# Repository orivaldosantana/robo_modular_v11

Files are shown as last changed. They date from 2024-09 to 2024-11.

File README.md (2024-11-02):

# Robô Modular - RM
Repositório de código, peças 3D e especificações básicas para o robô modular.

## Introdução

Esta versão é construída com Arduino, motor DC, baterias 18650 e ponte H L9110.
URA

## Peças 3D 
### STLs: 
* 1 x [Suporte Arduino](https://github.com/orivaldosantana/robo_modular_v11/blob/main/partes%203D/suporte%20arduino.stl) 
* 1 x [Base do suporte L9110](https://github.com/orivaldosantana/robo_modular_v11/blob/main/partes%203D/sup%20L9110%20base.stl)
* 1 x [Topo do suporte L9110](https://github.com/orivaldosantana/robo_modular_v11/blob/main/partes%203D/sup%20L9110%20topo.stl)
* 2 x [Suporte Motor DC](https://github.com/orivaldosantana/robo_modular_v11/blob/main/partes%203D/suporte%20motor%20v2.stl)
* 1 x [Chapa Modular 7x7](https://github.com/orivaldosantana/robo_modular_v11/blob/main/partes%203D/chapa%207x7.stl) 
* 2 x [Tira Modular 7x1](https://github.com/orivaldosantana/robo_modular_v11/blob/main/partes%203D/tira%207%20furos.stl) 
* 1 x [Caixa ultrassom](https://github.com/orivaldosantana/robo_modular_v11/blob/main/partes%203D/caixa%20ultrassom.stl)
* 1 x [suporte da caixa do ultrassom](https://github.com/orivaldosantana/robo_modular_v11/blob/main/partes%203D/suporte%20caixa%20ultrassom.stl)
* 4 x [Espaçador de 32 mm](https://github.com/orivaldosantana/robo_modular_v11/blob/main/partes%203D/espa%C3%A7ador%2032mm.stl)
* 2 x [Espaçador de 28 mm](https://github.com/orivaldosantana/robo_modular_v11/blob/main/partes%203D/espa%C3%A7ador%2028mm.stl)
* 1 x [Suporte para o sensor de linha](https://github.com/orivaldosantana/robo_modular_v11/blob/main/partes%203D/suporte%20sensor%20linha.stl)
* 1 x [Suporte roda boba](https://github.com/orivaldosantana/robo_modular_v11/blob/main/partes%203D/roda%20omni/sup%20omni.stl)
* 1 x [Roda Omni](https://github.com/orivaldosantana/robo_modular_v11/tree/main/partes%203D/roda%20omni)

### Editaveis no OnShape
## Montagem
* [Link para a montagem](https://cad.onshape.com/documents/1797a3ca0f50067e5b2f7467/w/d2fdd87127a878d32b85a5d1/e/55e155fb02a23330101a4e5d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)

Cima MD

MD

MD

MD

## Montagem Motores 
* [Preparação dos motores DC](https://youtu.be/uoehkZviNMs)
* [Montagem dos motores DC](https://youtu.be/0yrsRWZnIXw)

### Parafusos e complementares 
Entre chassis e suporte Arduino 
* 6 M4 de 12 mm 
* 6 porcas M4 

Entre chassis e suporte ultrassônico 
* 2 M4 de 12 mm 
* 2 porcas M4

Suportes dos sensores de linha 
* 2 M4 de 12 mm 
* 2 porcas M4

Entre chassis e suportes dos sensores de linha 
* 4 M4 de 12 mm
* 4 porcas M4

Suporte dos motores 
* 4 M3 de 28 mm 
* 4 porcas M3

Suporte L9110
* 2 M3 de 10 mm
* 2 porcas M3
  
Suporte Arduino
* 2 M4 de 18 mm
* 2 M4 de 12 mm 
* 4 porcas M4

Chassis e suporte roda boba 

Suporte ultrassônico 
* 2 M4 de 12 mm 
* 2 porca M4

Total aproximado 
* 18 M4 de 12 mm
* 2 M4 de 18 mm 
* 20 porcas M4

## Partes Eletrônicas e Outras 
| Link e Descrição | Qt. | Preço aproximado (R$) |
| --- | --- | --- |
| [20 CM 40 P DuPont cabo fêmea-fêmea, jumpers](https://pt.aliexpress.com/item/32847418999.html) | 1 | 10,00 | 
| [Arduino](https://pt.aliexpress.com/item/1005007512352122.html) | 1 | 35,00 |  
| [Motor DC TT de 3 a 12v com Roda](https://pt.aliexpress.com/item/32851946942.html ) | 2 | 30,00 | 
| [Ponte H L9110](https://pt.aliexpress.com/item/32893555258.html) | 1 | 4,00 |
| [Carregador portátil para celular, 5V 1A 2x18650 Caixa de Bateria](https://pt.aliexpress.com/item/33011621183.html) | 1 | 5,00 |
| [Baterias 18650 4.2v](https://produto.mercadolivre.com.br/MLB-717637625-kit-12-bateria18650-li-ion-8800mh-42v-lanterna-tatica-led-_JM) | 2 | 20,00 |
| [Sensor Ultrassom](https://pt.aliexpress.com/item/1005006140660054.html) | 1 | 10,00 | 
| [Sensor de Linha](https://pt.aliexpress.com/item/32837015888.html) | 2 | 10,00 | 
| Parafusos e outros |  | 5,00 |
| Filamento, cerca de 200 gramas| | 20,00 | 
| Despesas com envio (valor aproximado) | | 50,00 | 

O **total** por robô deve ficar em torno de: 200,00 (Em 2024) 

Observação: Ao comprar em quantidade é possivel que o custo do envio fique muito baixo ou até sem custo. 

## Códigos 
* [Sensor de Linha](https://github.com/Natalnet/lib_ura_esp/blob/master/ESP32/LineSensor/README.md)
* [Sensor de Distância](https://github.com/Natalnet/lib_ura_esp/tree/master/ESP32/UltrasonicSensor)
* [Sensor LDR](https://github.com/Natalnet/lib_ura_esp/tree/master/ESP32/LDR)

## Vídeos 
* [Visão geral das peças do robô URA desmontado](https://youtu.be/LthsH-N7xbM)
* [Apresentação resumida do hardware do robô educacional URA](https://youtu.be/fhzjdgP7kzs)
* [URA: Como controlar motores DC com MicroPython e ESP](https://youtu.be/Zrb4ya5w_Og)
* [IoT: Como gravar o firmware MicroPython no ESP?](https://youtu.be/F11Zw-0OYhw)
* [Controlando um robô de qualquer lugar do mundo](https://youtu.be/kUujN_RainY)
* [Controlando vários robôs do URA ao mesmo tempo](https://youtu.be/dd7foZvS9JI)
* [Versão inicial do software do robô URA para programação com processamento de linguagem natural](https://youtu.be/SiEE2sVo_tg) 
* [Sensor LDR](https://youtu.be/Xb-_oG65H2I)

## Mais fotos 

ura5

ura4

ura2

ura3

ura8

## TODO
* Organizar o código do seguidor de linha 

## Atualizações realizadas 
1. Suporte motor DC
2. Suporte roda omni 
3. Soporte ultrassom
4. Códigos para testar o ultrassom
5. Códigos para testar as rodas

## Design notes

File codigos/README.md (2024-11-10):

# Documentação do Código

Vídeo explicando o funcionamento do Fujão: https://youtu.be/eueH48s2pj8 

## Configuração dos Pinos 

### Ponte H 

| Ponte H L9110  | Arduino | 
| --- | --- |
| B-1A | 13 | 
| B-1B | 12 |
| G  | GND  | 
| VCC | Vin (5v) | 
| A-1A | 11 | 
| A-1B | 10 | 

Motor A - Esquerdo  
* Velocidade PWM do Motor A --> A_IA  --> 11 
* Direção do Motor A        --> A_IB  --> 10

Motor B - Direito 
* Velocidade PWM do Motor B --> B_IA  -->  13
* Direção do Motor B        --> B_IB  -->  12 

### Sensor de distância (Ultrassom) 

| Sensor de distância frontal | Arduino |
| --- | --- |
| GND | GND  | 
| Trig  | 9 | 
| Echo  | 8 |
| Vcc | 5v | 

| Sensor de distância esquerdo | Arduino |
| --- | --- |
| GND | GND  | 
| Trig  | 7 | 
| Echo  | 6 |
| Vcc | 5v | 

| Sensor de distância direito | Arduino |
| --- | --- |
| GND | GND  | 
| Trig  | 3 | 
| Echo  | 2 |
| Vcc | 5v | 

### Sensores de Linha 

| Sensor de Linha Esquerdo | Arduino |
| --- | --- |
| G  | GND  | 
| V+ | 5v | 
| S  | 4 | 

| Sensor de Linha Direito | Arduino |
| --- | --- |
| G  | GND  | 
| V+ | 5v | 
| S  | 5 | 

## Robô Fujão 
O robô fujão foi projeto para correr em área livres, quando ele encontra alguma barreira ele tenta se afastar. O seu código foi desenvolvido com base na rede neural SOM (https://github.com/ect-comp/ml/blob/master/aulas/som.md) e contem 36 neurônios. A sua estrutura física é constituída de basicamente dois motores DC e três sensores ultrassônicos posicionados, uma na frente, outra na lateral esquerda e outra na lateral direita. 

SOM
Figura da rede SOM, fonte: https://link.springer.com/article/10.1007/s40747-022-00761-2 

O princípio de funcionamento do código do Fujão é ler os valores dos sensores de distância, buscar na rede neural a experiência que melhor representa estas leituras e reagir conforme a experiência aprendida pela rede neural. O processo de treinamento da rede neural consistiu em coletar situações especificas (leituras dos sensores) e criar representações destas situações na rede neural SOM. Considerando que cada situação da base de treinamento possui uma ação associada, após treinada, cada neurônio da rede foi associado a uma ações. A situação ou estado do robô é representado pela leitura dos sensores. As situações e as ações foram gravadas em uma base de dados (txt). A base foi organizada em 4 colunas, sendo as três primeiras para as leituras dos sensores e a quarta coluna para a ação do robô (andar para frente, girar para esquerda, girar para direita ou andar para trás). 

Exemplo de uma base de dados: 
```txt
13 4
0   0  0 r
20  0 20 r
20 20 20 r
10 40 68 d
10 20 68 d
68 68 20 e
68 40 20 e
68 68 68 f
20 68 20 f
20 40 20 r
68 40 20 e
20 40 60 f
68  0 68 e
68 10 68 e
``` 

### Fotos 

Fujão
Fujão
Fujão
Fujão

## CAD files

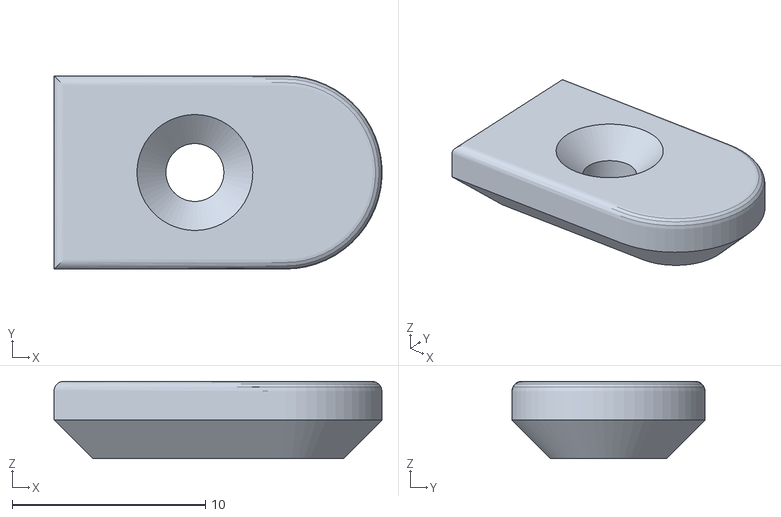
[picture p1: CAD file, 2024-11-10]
partes 3D/roda omni/tampa eixo suporte.stl
17.0 x 10.0 x 4.00

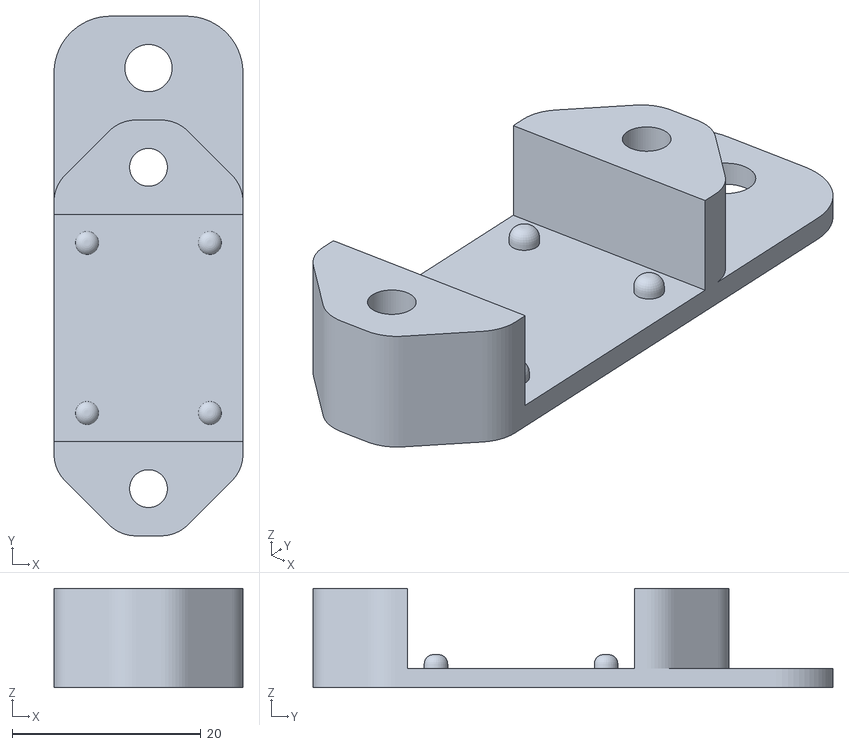
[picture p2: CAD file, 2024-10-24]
partes 3D/sup L9110 base.stl
20.0 x 55.0 x 10.5

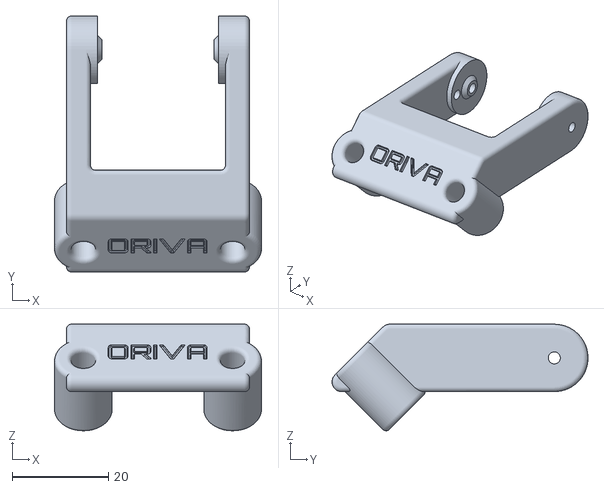
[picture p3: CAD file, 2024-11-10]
partes 3D/roda omni/sup omni.stl
43.0 x 53.2 x 22.1

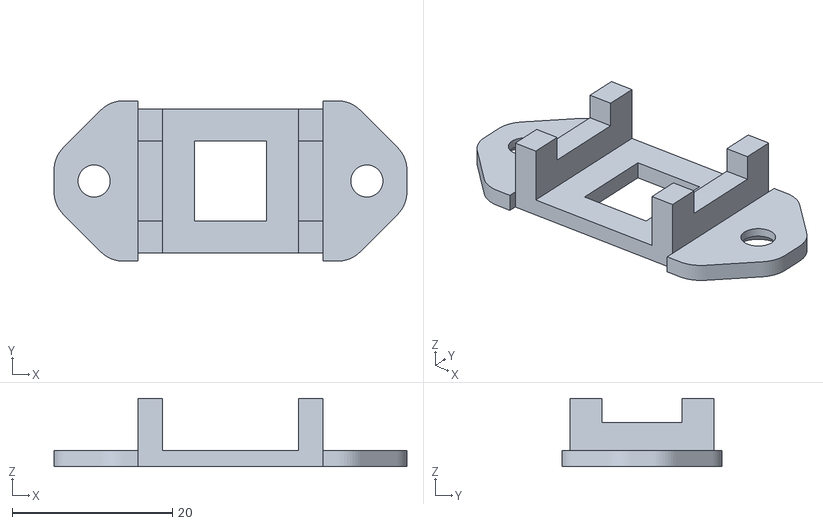
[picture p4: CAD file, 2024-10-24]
partes 3D/sup L9110 topo.stl
44.0 x 20.0 x 8.50

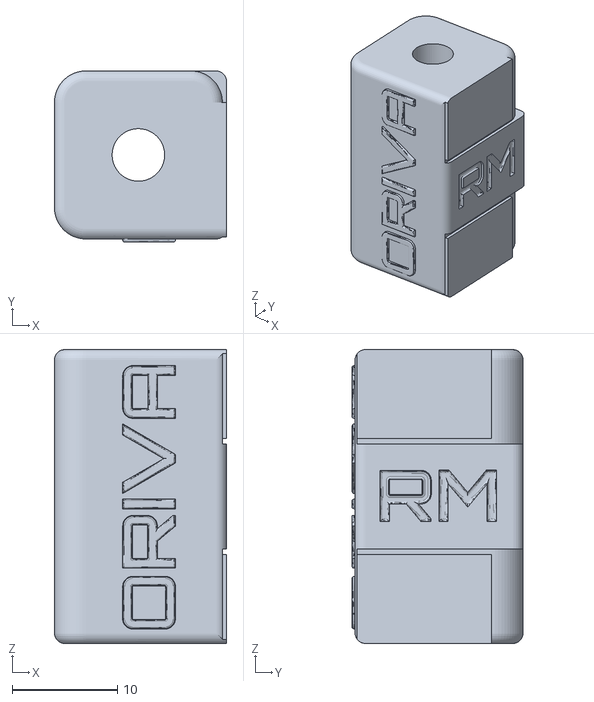
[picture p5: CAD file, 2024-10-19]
partes 3D/espaçador 28mm.stl
16.4 x 16.3 x 28.0

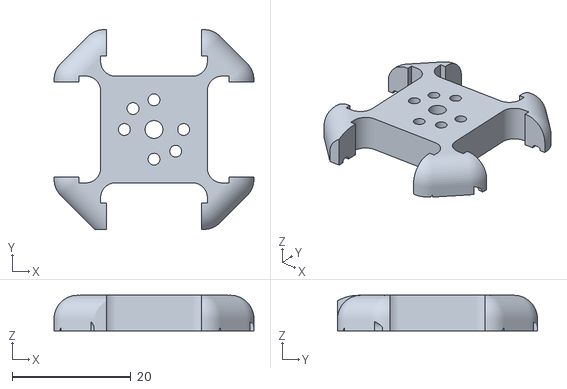
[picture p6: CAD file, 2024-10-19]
partes 3D/roda omni/suporte interno v2.stl
33.7 x 33.7 x 6.00

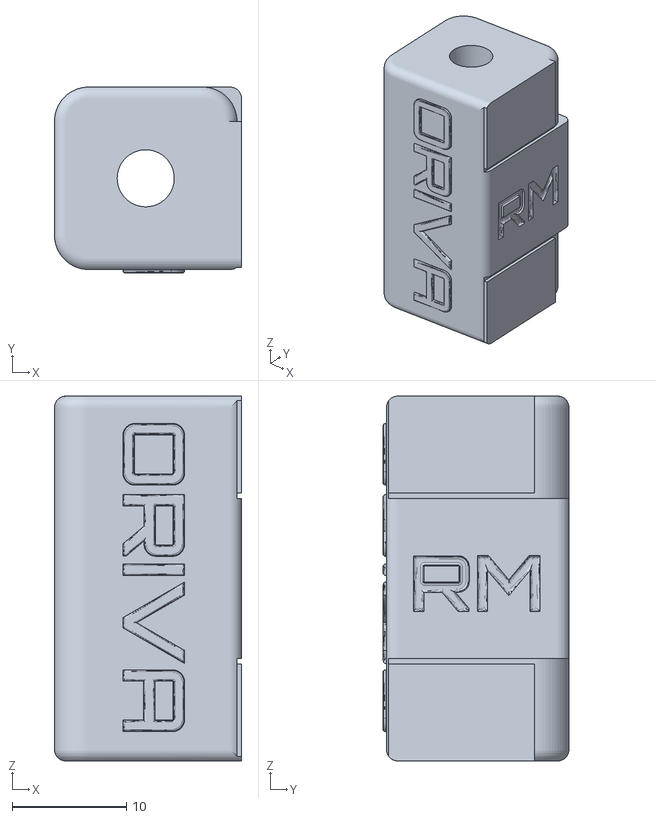
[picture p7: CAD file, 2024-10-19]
partes 3D/espaçador 32mm.stl
16.4 x 16.3 x 32.0

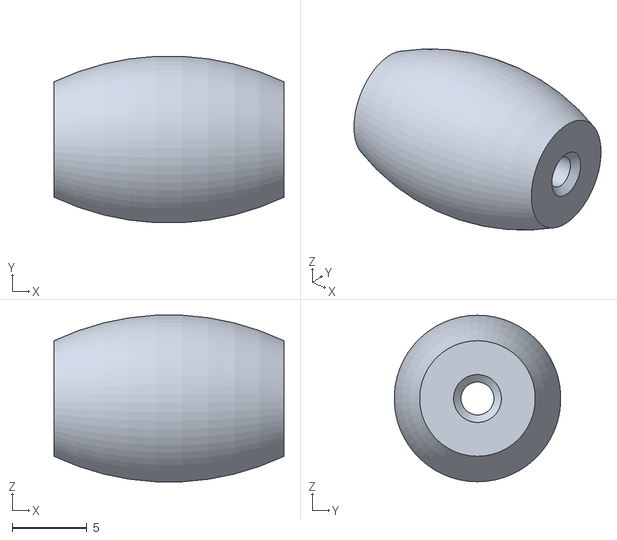
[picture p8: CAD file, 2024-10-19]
partes 3D/roda omni/mini roda.stl
15.4 x 11.1 x 11.2

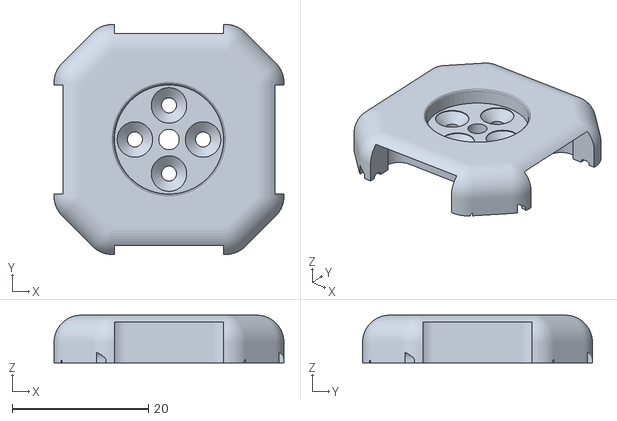
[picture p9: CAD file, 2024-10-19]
partes 3D/roda omni/Suporte externo.stl
33.7 x 33.7 x 7.00

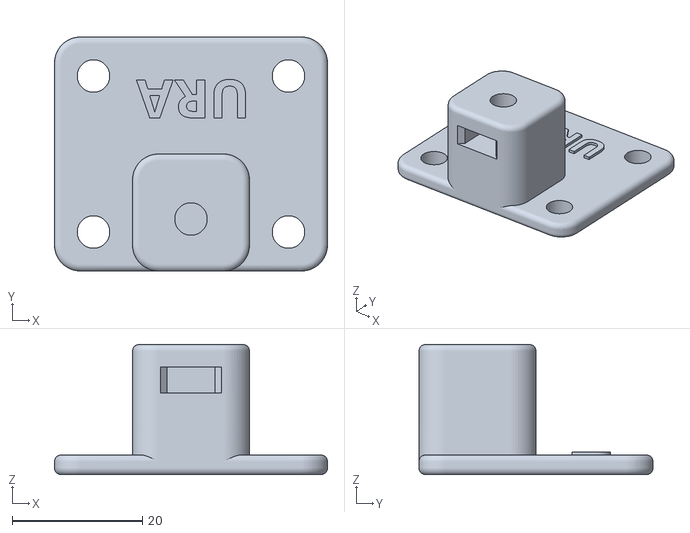
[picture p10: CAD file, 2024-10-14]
partes 3D/suporte roda boba.stl
42.0 x 36.0 x 20.0

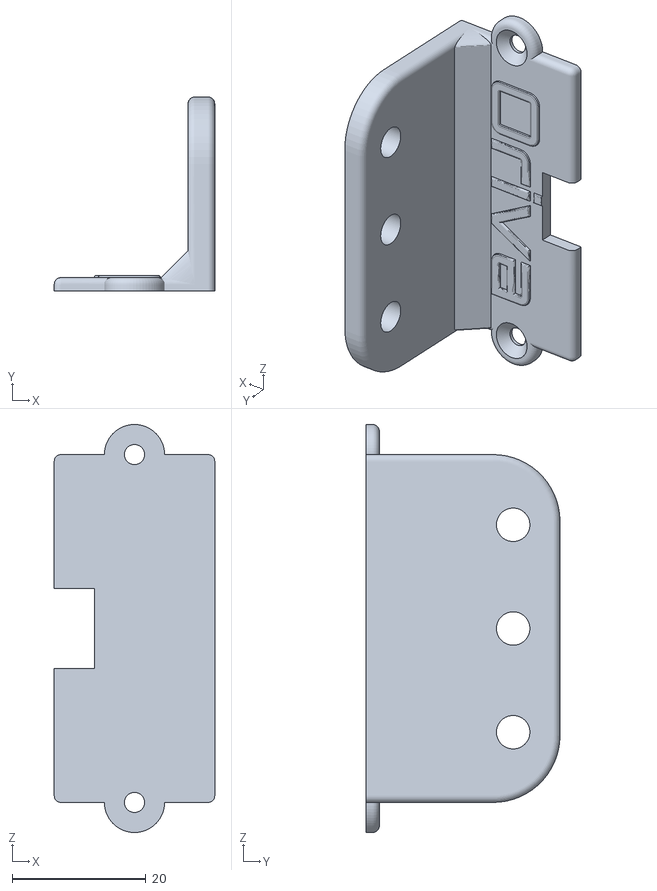
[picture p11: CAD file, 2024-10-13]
partes 3D/suporte caixa ultrassom.stl
24.0 x 29.0 x 61.0

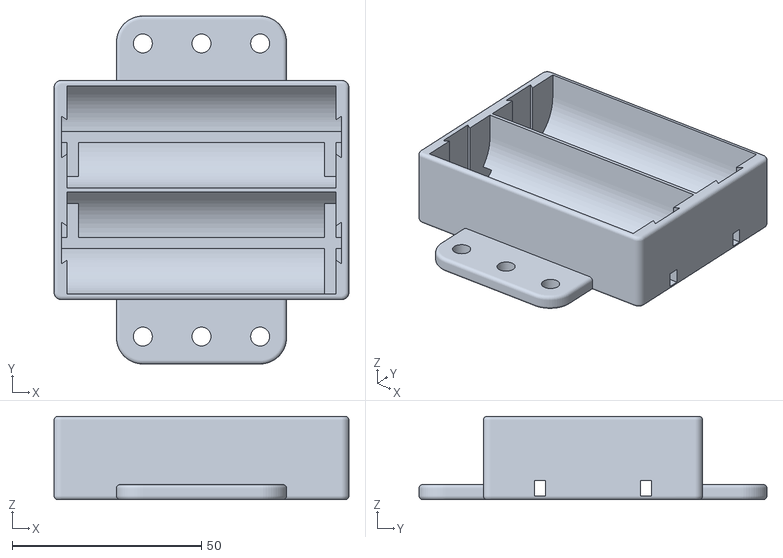
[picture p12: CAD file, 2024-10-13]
partes 3D/Bats 26650.stl
78.0 x 92.0 x 22.0

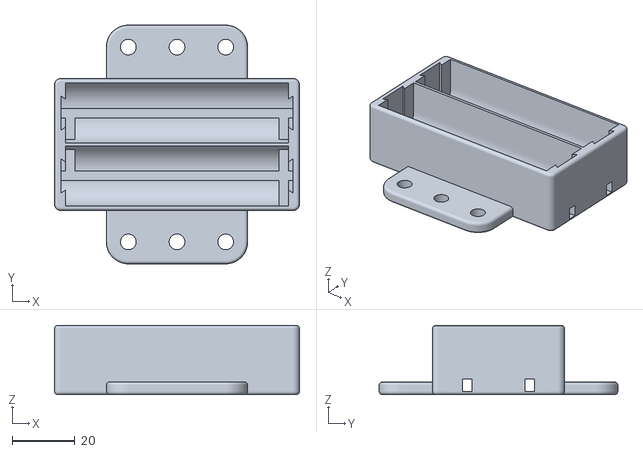
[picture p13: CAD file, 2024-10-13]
partes 3D/bats 18650.stl
78.0 x 76.0 x 22.0

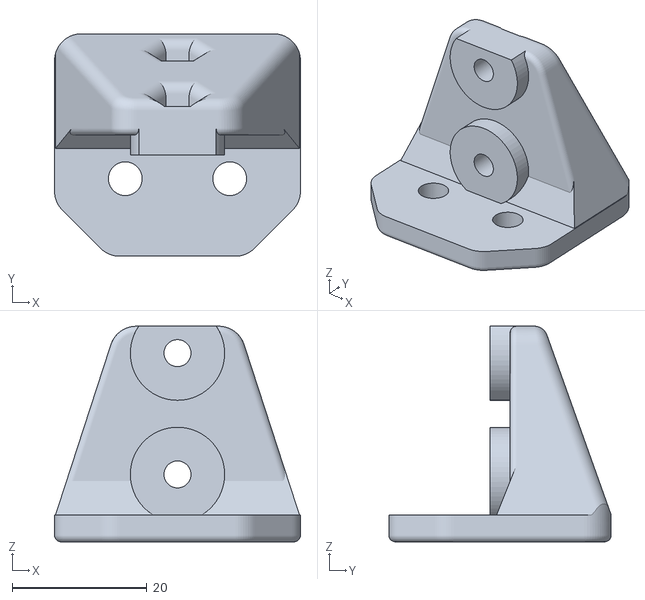
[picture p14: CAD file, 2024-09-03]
partes 3D/suporte motor v2.stl
36.5 x 33.0 x 32.0

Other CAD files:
partes 3D/chapa 7x7.stl
partes 3D/tira 7 furos.stl
partes 3D/suporte sensor linha.stl
partes 3D/caixa ultrassom.stl
partes 3D/suporte arduino.stl

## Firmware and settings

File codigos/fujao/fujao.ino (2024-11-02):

#include "l9110.h"
#include "RedeSOM.h"
#include "Ultrassom.h"


L9110 motoresRobo(11, 10, 13, 12);

Ultrassom usd(3,2); // ultrassom  
Ultrassom use(7,6); // ultrassom  
Ultrassom usf(9,8); // ultrassom frente 

int vSensores[3]; 

RedeSOM som;

void setup()
{
  Serial.begin(9600);
  usf.setup();
  use.setup();
  usd.setup();
}

void executaMovimento(char resposta){
  if(resposta == 'f'){
    motoresRobo.frente(255,40);
  }else if(resposta == 'r'){
    motoresRobo.re(255,40);
  }else if(resposta == 'e'){
    motoresRobo.esquerda(255,30);
  }else if(resposta == 'd'){
    motoresRobo.direita(255,30);
  }else{
    motoresRobo.parar();
  }
}

void testeMelhorResposta() {
  int vc[] = {18, 68, 22}; 
  Serial.println(som.melhorResposta(vc)); 
}

void movimentaComRedeSOM(){
  vSensores[0] = use.dist();
  vSensores[1] = usf.dist(); 
  vSensores[2] = usd.dist(); 
  
  char c = som.melhorResposta(vSensores); 
  Serial.print("Sensores: ");  
  for( int i=0; i <3; i++) {
    Serial.print(vSensores[i]);
    Serial.print(" "); 
  }
  Serial.println(c);   
  
  Serial.println("Movimento: ");
  Serial.println(c);

  executaMovimento(c);
  
}

void loop()
{
  movimentaComRedeSOM();

}

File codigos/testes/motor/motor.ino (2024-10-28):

#include "l9110.h"

L9110 motoresRobo(11, 10, 13, 12);

void setup()
{
  Serial.begin(9600);
}

void loop()
{
  int tempoParado = 2000;
  Serial.println("Frente");
  motoresRobo.frente(255,1000);
  motoresRobo.parar();
  delay(tempoParado);
  Serial.println("Re");
  motoresRobo.re(255,1000);
  motoresRobo.parar();
  delay(tempoParado);
  Serial.println("Esquerda");
  motoresRobo.esquerda(255,1000);
  motoresRobo.parar();
  delay(tempoParado);
  Serial.println("Direita");
  motoresRobo.direita(255,1000);
  motoresRobo.parar();
  delay(tempoParado);
  Serial.println("Parar");
  motoresRobo.parar();
  delay(tempoParado);
}

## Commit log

2024-09-03 primeiras peças
    [caixa ultrassom.stl, chapa 7x7.stl, espaçador 28mm.stl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]
2024-10-13 Update suporte caixa ultrassom.stl
    [suporte caixa ultrassom.stl]
2024-10-14 Create suporte roda boba.stl
    [suporte roda boba.stl]
2024-10-19 roda omni
    [Suporte externo.stl, espaçador 28mm.stl, espaçador 32mm.stl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]
2024-10-24 Parte 3D - L9110
    [sup L9110 base.stl, sup L9110 topo.stl]
2024-10-28 teste motores
2024-11-10 roda omni up
    [sup omni.stl, tampa eixo suporte.stl]
